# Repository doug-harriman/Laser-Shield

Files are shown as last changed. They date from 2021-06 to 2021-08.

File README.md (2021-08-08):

# Laser-Shield
Design documentation for a laser shield for the [Sainsmart Genmitsu 5.5W Laser Module](https://www.sainsmart.com/collections/cnc-machines/products/sainsmart-blue-laser-module-kit) mounted to a [Sainsmart Genmitsu 3018 Pro CNC Mill](https://www.sainsmart.com/collections/cnc-machines/products/sainsmart-genmitsu-cnc-router-pro-diy-kit).  See my [3018 Mill](https://github.com/doug-harriman/3018-Mill/) repository for general information about using the mill and laser.

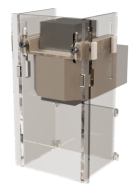
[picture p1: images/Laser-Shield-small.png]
Laser Shield Rendering

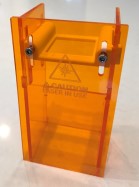
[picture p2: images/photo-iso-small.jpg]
Laser Shield Photo


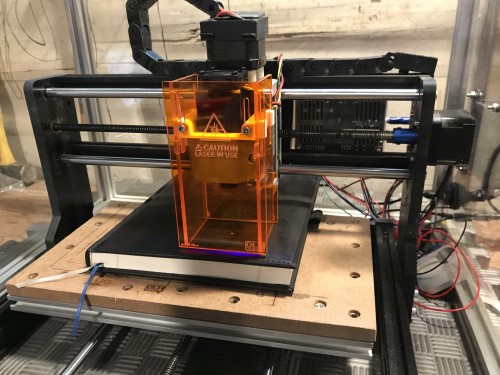
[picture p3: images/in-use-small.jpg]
Laser Shield In Use


# BOM
|Part|Count|Material|
|:---| :-: |---|
|Mount| 1 | PLA  |
|Front| 1 |Laser Shielding|
|Side| 2 |Laser Shielding|
|Rear| 1 |Laser Shielding|
|M3 Threaded Insert| 2 | Brass | 
|M3x6 Screw| 2 | Stainless |

# Part Documentation
All parts were designed in Fusion360, see the [cad](cad/) directory for CAD files.

Assembly [STL](cad/laser-shield-v25.stl)

## Mount 
The shield mount was 3D printed on a [Creality Ender3 Pro](https://www.creality3dofficial.com/products/creality-ender-3-pro-3d-printer) with [Hatchbox white PLA](https://www.amazon.com/gp/product/B00J0GMMP6/).

The STL was created in Fusion360 and sliced with [Cura](https://ultimaker.com/software/ultimaker-cura) 4.8.0 with the default settings for the Ender3 Pro and PLA, and a slice height of 0.12 mm.  Design files:
* [STL](cad/Shield-Mount.stl)
* [G-Code](mfg/Shield-Mount.gcode) for 3D printer

## Front, Rear & Sides
The front, rear and side shields were machined out of a 300mm x 300mm sheet of laser shielding material on the Sainsmart Genmitsu 3018 Pro.

STL for:
* [Front](cad/Shield-Front.stl)
* [Sides](cad/Shield-Side.stl)
* [Rear](cad/Shield-Rear.stl)

### Material
The laser shielding material is an transparent orange plastic which I believe to be cast acrylic. The laser wavelength is 445nm (blue).  Orange filters blue light eliminating most of the optical power.  Material was purchased from [J-Tech Photonics](https://jtechphotonics.com/?product=445nm-laser-shielding).

### Machining
* Tool: [1.0 mm diameter, 2 flute flat end mill](https://github.com/doug-harriman/3018-Mill/blob/main/milling/tools-n-bits/tools-n-bits.md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).
* Feeds & Speeds
  * Spindle speed was at max using the stock 775 3018 Pro spindle motor.  This is approximately 5000 RPM.
  * Feed rates
    * Cutting: 600 mm/min
    * Positioning: 1500 mm/min
    * Depth of cut: 0.25 mm 
* Tool Path
  * Tool path used was a simple 2D contour, conventional (right) milling.  Details available in the Fusion360 design files.
  * G-Code 
    * [Front](/mfg/shield-front.nc) 
    * [Sides](mfg/shield-sides.nc) (machined together)
    * [Rear](mfg/shield-rear.nc)

## Threaded Inserts
M3 brass threaded inserts.  Purchased from [Amazon](https://www.amazon.com/gp/product/B07H2RWRW4/).

Inserts were pressed into the Mount with a soldering iron.  Pressed until they extended ~0.25 mm beyond the face of the Mount, then the Mount was pressed onto a flat surface to get the insert face flush and level with the Mount face.

For more detail on dimensioning and techniques for threaded inserts see the Hackaday how-to on [Threading 3D Printed Parts](https://hackaday.com/2019/02/28/threading-3d-printed-parts-how-to-use-heat-set-inserts/).

## M3 Screws 
M3x6 hex socket head screws. Purchased from [Amazon](https://www.amazon.com/gp/product/B014OO5KQG).

# Artwork
All artwork was created in Inkscape and converted from SVG to G-Code with the Lasertools Inkscape Extension.  See my [3018 Mill](https://github.com/doug-harriman/3018-Mill/) project for more information on the tools and processes.

Portions of the artwork were obtained from the Open Source community.  See the [Artwork Source](artwork/artwork-source.md) documentation for more details.

Laser etch parameters (see 3018 Mill project for speed & power test data)
* Etching speed: 800 mm/min (infill & perimeter)
* Infill laser power: 40% (400 on Sainsmart system)
* Perimeter laser power: 60% (600 on Sainsmart system)
* Beam width: 0.2 mm
* Contour tolerance: 0.1 mm

# Future Improvements
* Redesign rear shield to mount fan for air assist for cutting.
  * Have a small fan on hand from [Amazon](https://www.amazon.com/gp/product/B0755BY9RH/). 
* Reduce length of shield mount.  Interferes with top of Z-axis mount when in extreme +Z position.

# Links
Other links to this project
* [YouTube](https://www.youtube.com/watch?v=rP4ZKo0Rn4E)
* [Thingiverse](https://www.thingiverse.com/thing:4885034)

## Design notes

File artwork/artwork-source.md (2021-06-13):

# Artwork

## Creation
Front Shield artwork contains two icons that were obtained from the Open Source community:
* Laser Symbol Icon made from [Icon Fonts](http://www.onlinewebfonts.com/icon) is licensed by CC BY 3.0.
* Caution Symbol from [SVG Repo](https://www.svgrepo.com/svg/33116/caution)

The laser symbol was fit inside of a triangle created in Inkscape. 

## Output
(Note: Font does not seem to render correctly on GitHub)

Artwork

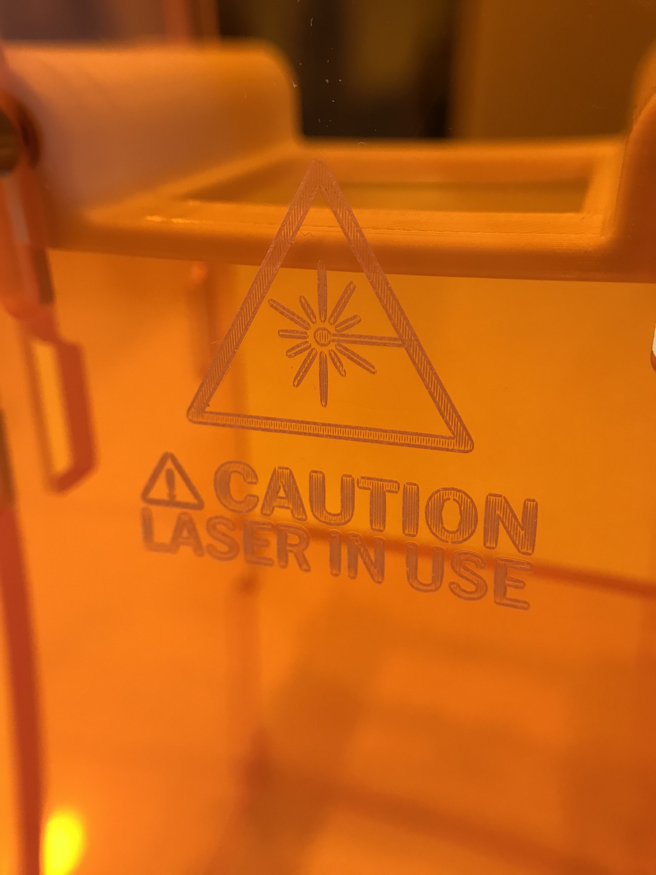
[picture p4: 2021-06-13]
images/artwork-closeup.jpg

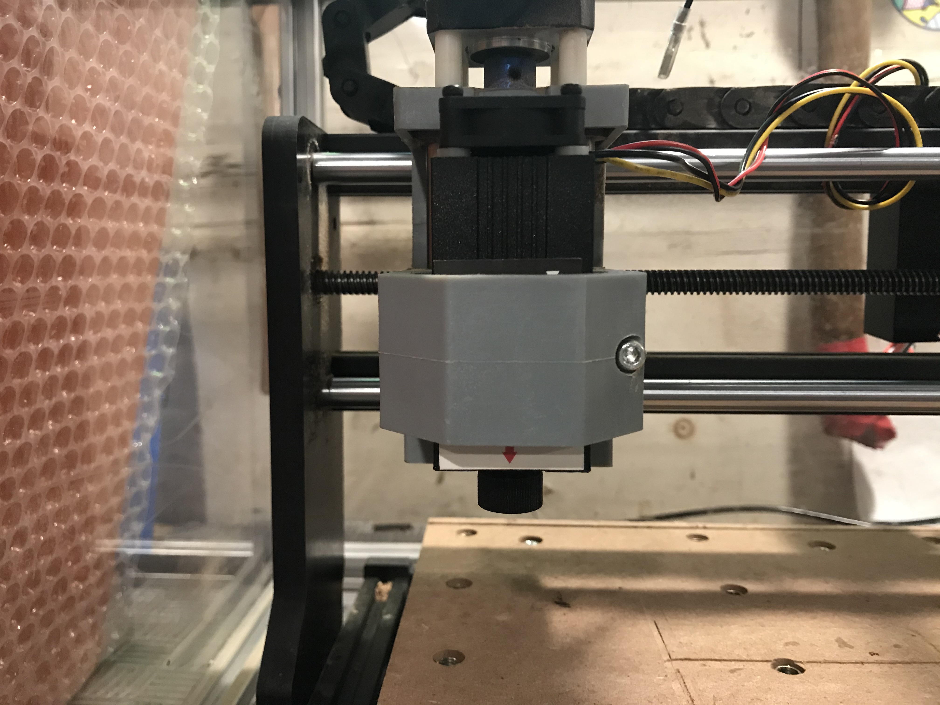
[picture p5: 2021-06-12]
images/spindle-holder-front.jpg

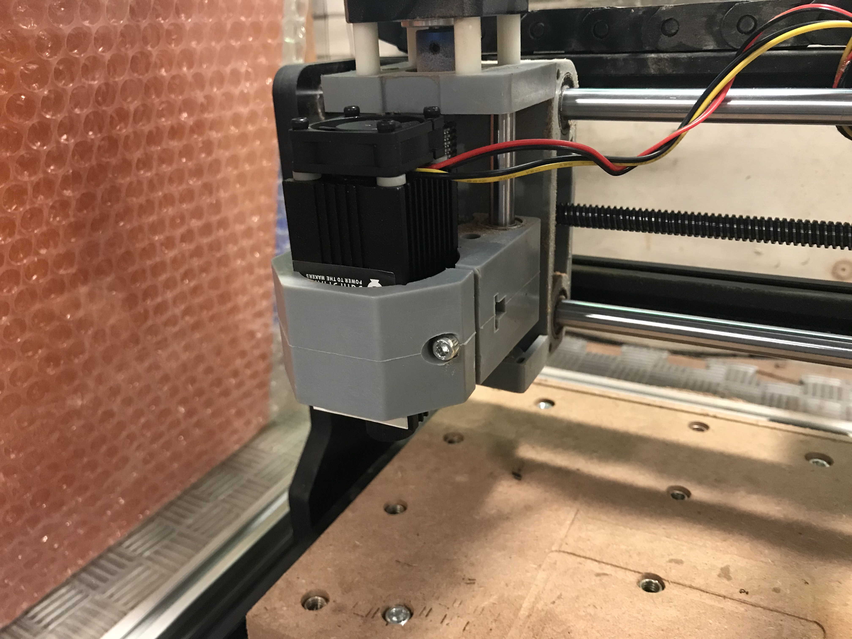
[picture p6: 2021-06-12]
images/spindle-holder-iso.jpg

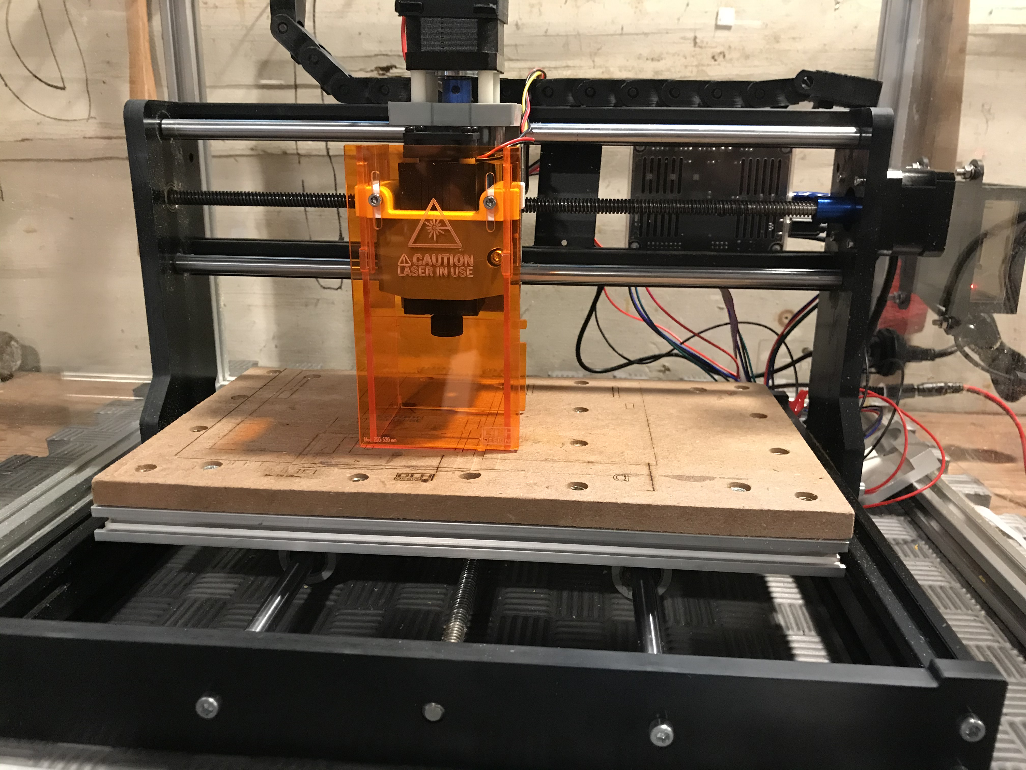
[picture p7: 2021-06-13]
images/on-machine.jpg

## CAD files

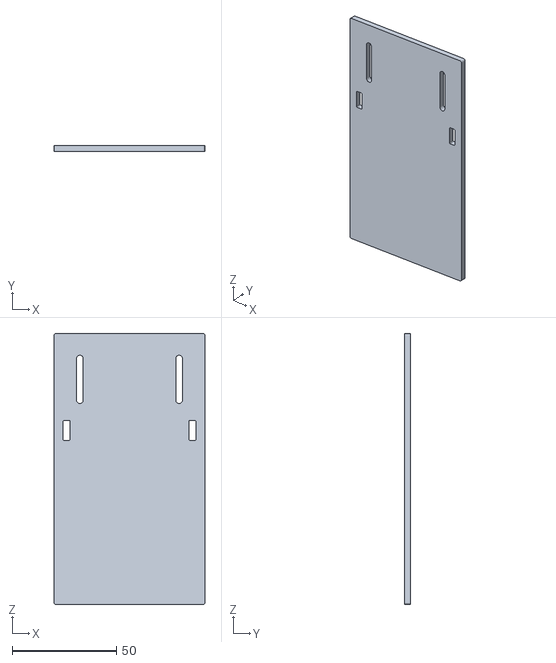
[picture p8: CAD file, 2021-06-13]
cad/Shield-Front.stl
72.4 x 3.00 x 130.0

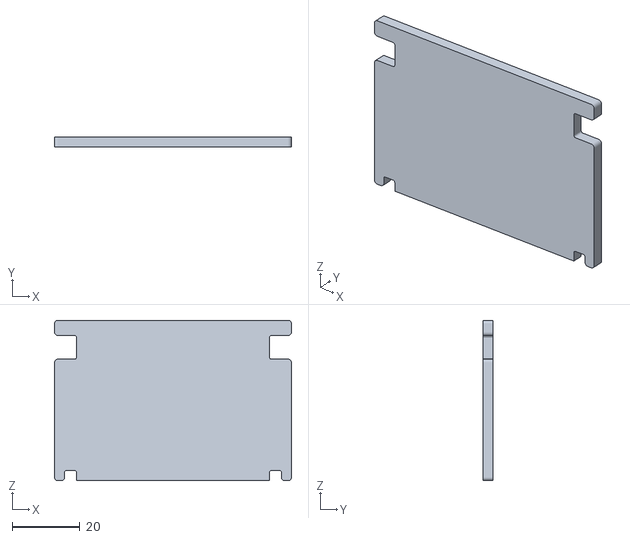
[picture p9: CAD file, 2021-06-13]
cad/Shield-Rear.stl
70.2 x 3.00 x 47.5

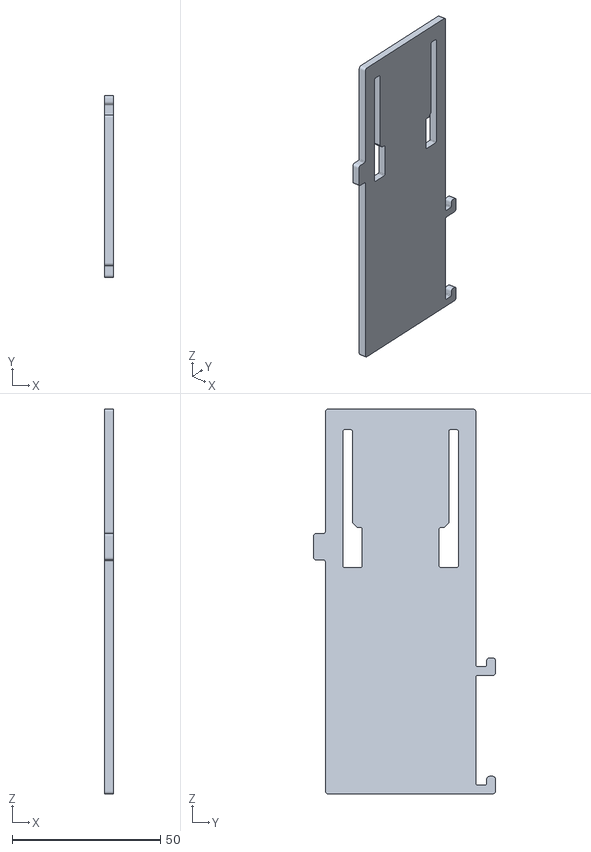
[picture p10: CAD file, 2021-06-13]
cad/Shield-Side.stl
3.00 x 61.5 x 130.0

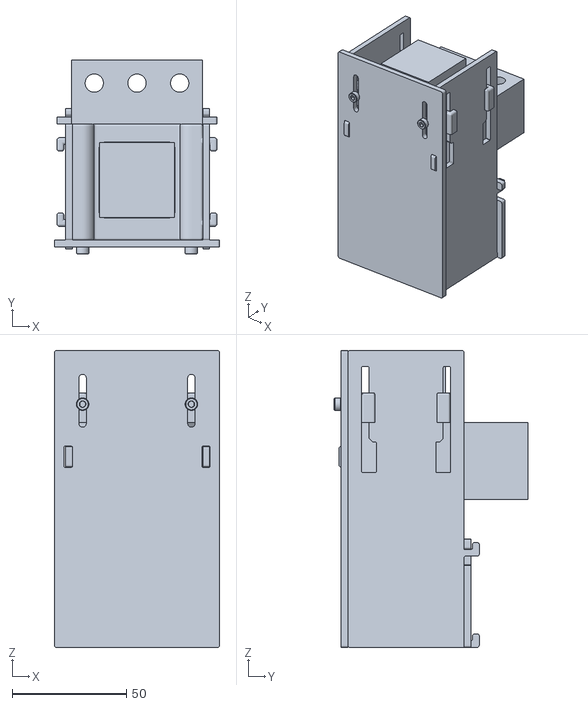
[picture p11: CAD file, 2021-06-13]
cad/laser-shield-v25.stl
72.4 x 84.7 x 130.0

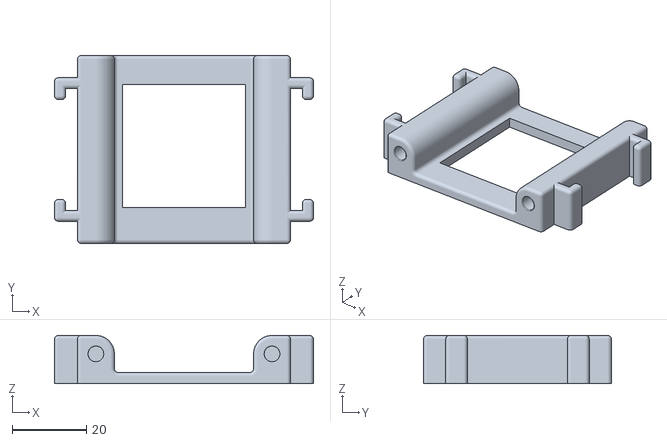
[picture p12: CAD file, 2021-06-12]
cad/Shield-Mount.stl
70.0 x 50.8 x 13.0

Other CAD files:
cad/Laser-Shield-v25.f3d

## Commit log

2021-06-12 Captured images and shield mount mfg files.
    [Shield-Mount.stl]
2021-06-13 Added STL of full system.
    [laser-shield-v25.stl]
2021-06-13 Capture Fusion360 CAD for design.
    [Laser-Shield-v25.f3d]
2021-06-13 Added individual part STL.
    [Shield-Front.stl, Shield-Rear.stl, Shield-Side.stl]
2021-06-13 Moved mount STL to CAD dir.
    [Shield-Mount.stl]
